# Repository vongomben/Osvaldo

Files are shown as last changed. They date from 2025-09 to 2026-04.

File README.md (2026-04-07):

# Osvaldo
Osvaldo is aimed to make ethreal messages physical, from the meshiverse:

Osvaldo

It all stems from **[a thought](https://www.reddit.com/r/meshtastic/comments/1d07e7j/meshtastic_thermal_printer_ticker_tape_node/) I had a year ago: how to save and somehow record these ephemeral-ethereal messages in our absence?**

Attach a printer to a meshtastic radio and see the messages coming one after another, a real physical representation of the conversations.

This project was an excuse to see how far a meshtastic radio could be integrated into a more distributed and complex system. 

A number of things can be built from here, including - in addition to the printer from which we start - **a small bot capable of field operations**, or even **a very simple BBS** (Bulletin board system) **based on microntrollers**. 

The idea of the printer is itself an hommage to the [Little Printer from Berg](https://www.failory.com/cemetery/berg) [Youtube Video](https://www.youtube.com/embed/IlC5taBgLp0?si=3HXCBTyb_Gr8--oA)

As for the Meshbot, this project updates several ideas and limits and scenarios in a new way. 
We are not making "printer of the internet", you could easily do that in many other ways-
Osvaldo is not even connected to the internet (and for this reason, I guess it doesn't event know the time and date). 
Osvaldo is connected to the Mesh. 

He receives messages and prints them. 
I could possibly add many features to this, which is an ongoing project. 
One is the Battery, maybe even solar powered. 
Another is exposing a Captive Portal that allows you to control Osvaldo via the phone (wifi): eyes (colours), texts, QR code of the Meshtastic Channel Osvaldo is listening to.

The future holds many challenges in front of us, lets see. 

### But What is Osvaldo doing right now?

- Osvaldo is a node in the Mesh
- Prints the received messages and make some funny LED patterns

### Hardware

- a meshtastic radio (I am using a [XIAO ESP32S3 & Wio-SX1262 Kit for Meshtastic & LoRa](https://www.seeedstudio.com/Wio-SX1262-with-XIAO-ESP32S3-p-5982.html?)
- a second radio from which to send data (paired with a cell phone)
- a microcontroller (Xiao ESP32S3)
- a voltage converter
- 2 switches (I want to be able to turn off the printer and possibly turn off the Xiao ESP32S3 managing the LEDS & printer behaviours)
- a strip of WS2812 LEDs
- 2 kikcback diodes (or Schottky diodes) because we will need to access both boards (the xiao-radio and tha xiao that manages the printer) without powering up the rest / interfere with the circuits. 
- two [Xiao Grove Shields](https://wiki.seeedstudio.com/Grove-Shield-for-Seeeduino-XIAO-embedded-battery-management-chip/) (for purely educational purposes - I'm getting old. You can skip them if you want to make you project tynier and save money. 

### Software side, we use:
- [meshtastic web flasher](https://flasher.meshtastic.org/)
- [meshtastic console](https://client.meshtastic.org/)
- [Arduino IDE with ESP32 core](https://wiki.seeedstudio.com/xiao_esp32s3_getting_started/#software-preparation)
- [Meshtastic's Protobuf library for Arduino](https://github.com/meshtastic/Meshtastic-arduino)
- [Adafruit Thermal Printer Library](https://github.com/adafruit/Adafruit-Thermal-Printer-Library) 

## 1) Flashing Radio n° 1

Visit [meshtastic web flasher](https://flasher.meshtastic.org/) and follow the instructions. 

flashing

## 2) Configuring the Radio

While you can go on from here using the Android or iOS app, I'll stick with the [meshtastic console](https://client.meshtastic.org/). 
We are going to **define its Serial pins** (based on Xiao's pin mapping) and **enable protobuf communication**. 

configuring

Since I'm using the [Xiao Grove Shields](https://wiki.seeedstudio.com/Grove-Shield-for-Seeeduino-XIAO-embedded-battery-management-chip/) I'm also sharing this useful image of the pin mapping. 

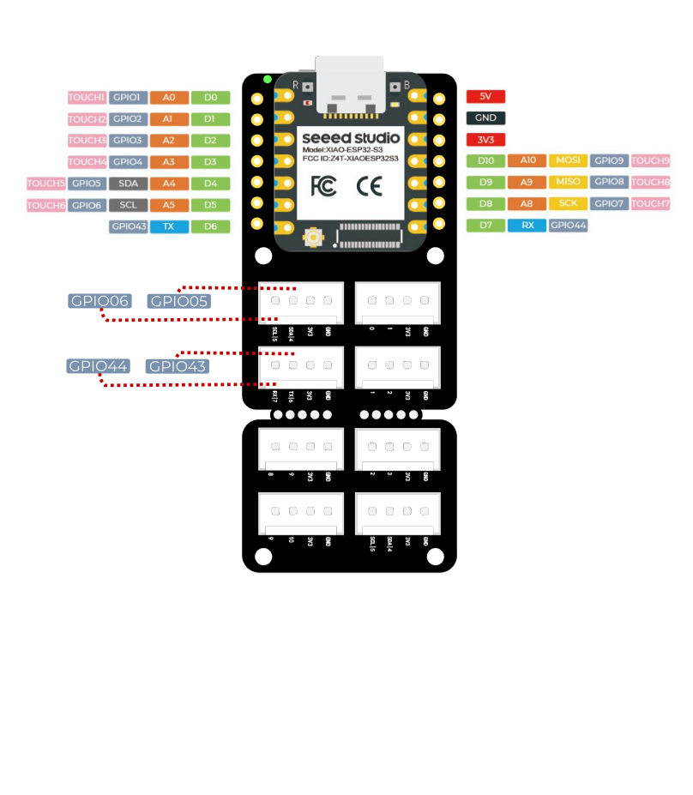
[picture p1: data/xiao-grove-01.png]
Xiao Grove Shield


## 3) Listening to the Serial Port using Protobuf from another Xiao

Let's connect the two boards in this way. 
Important TX is going to RX, and viceversa. Do not connect 3V3 for now. 

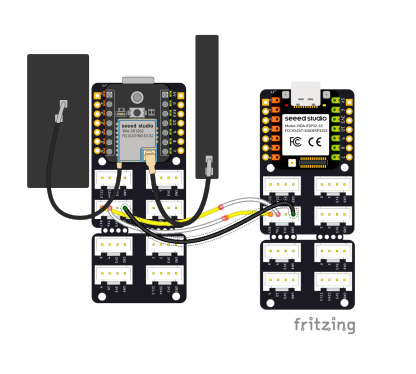
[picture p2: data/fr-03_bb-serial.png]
serial


In order to have a cable for the serial communication I changed a grove connector making it usable changing TX to RX and vice versa. 

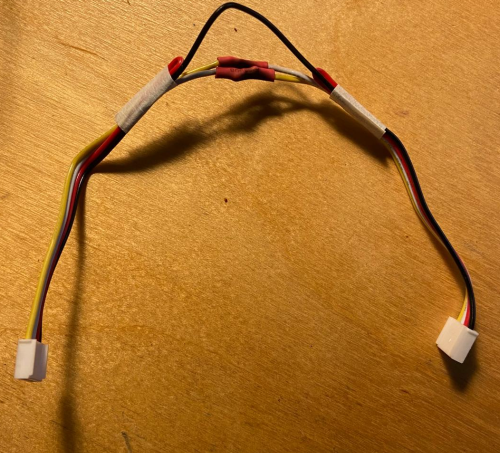
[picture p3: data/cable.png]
special cable


After installed the library, we can run this code in order to read whichever is passing via the serial and read all the nodes received in the serial port. Don't worry: we are going to fine tune this code in order to do less.

## 4) Let's attach the priter!

Hook up the printer following these instructions

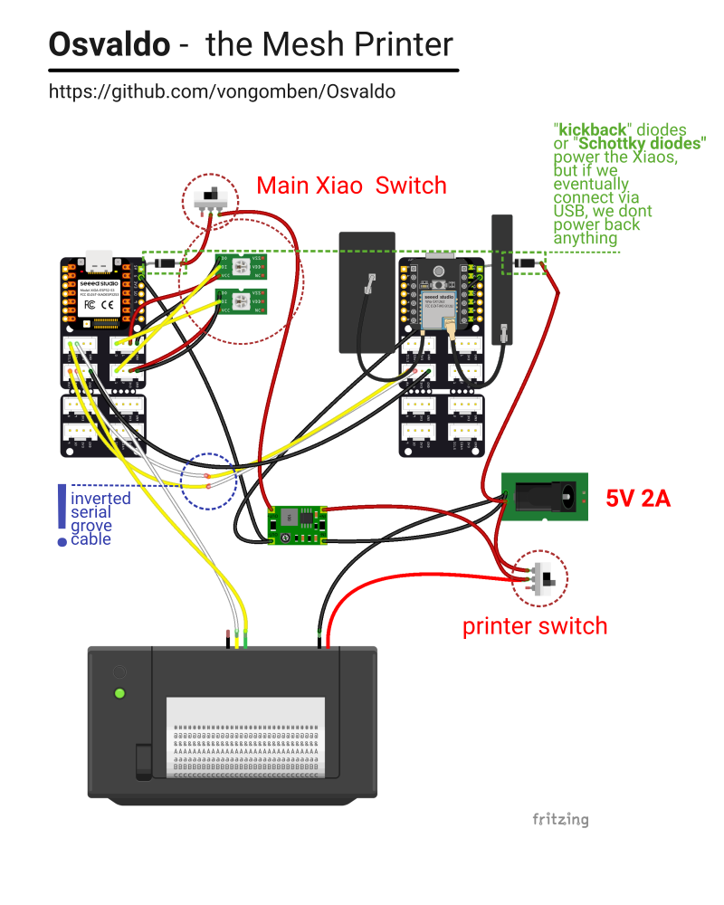
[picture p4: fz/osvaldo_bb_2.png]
printer


## 5) Print and assemble Osvaldo

I have used some trasparent PLA to create the eyes. Inside I've put the LEDs. 
Nice. 
You can find the stl files of this version in the folder. You should print "eye-cover.stl" in transparent PLA. All the rest is up to you for color or material.  

You have to solder the LEDs in order to make them stay in the eye. 

led

##  Test Osvaldo

Before connecting Osvaldo to the Mesh we have to test if it's printing and the LEDs are working:
- Check the LEDs
- check connections (passive listener)
- Test the final printer!

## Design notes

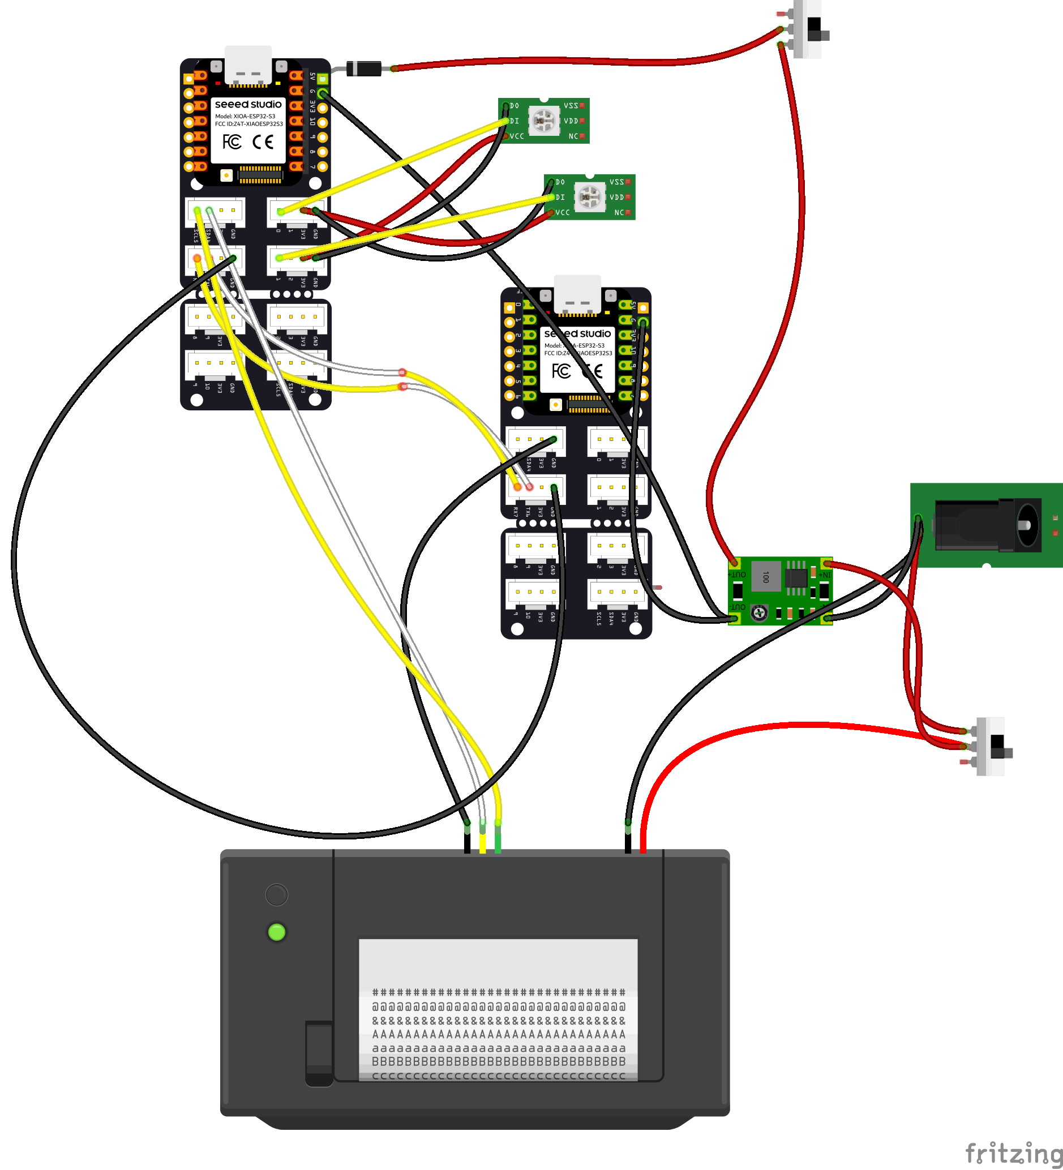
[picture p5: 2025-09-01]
fz/osvaldo_bb.png

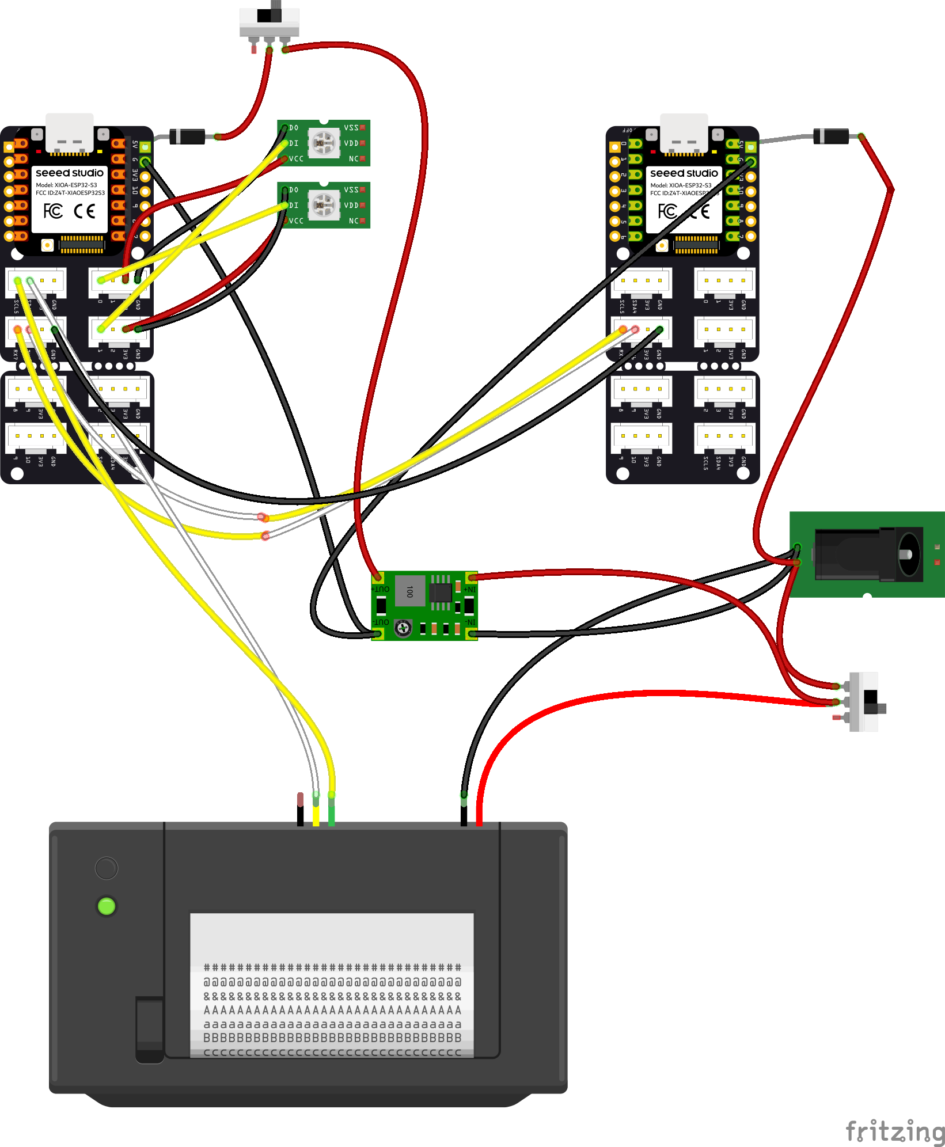
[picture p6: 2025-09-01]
fz/osvaldo_bb_3.png

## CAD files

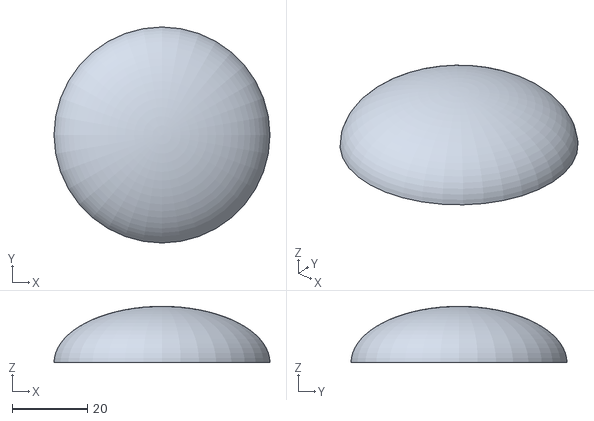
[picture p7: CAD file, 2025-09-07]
data/stl/eye-cover.stl
57.5 x 57.5 x 15.0

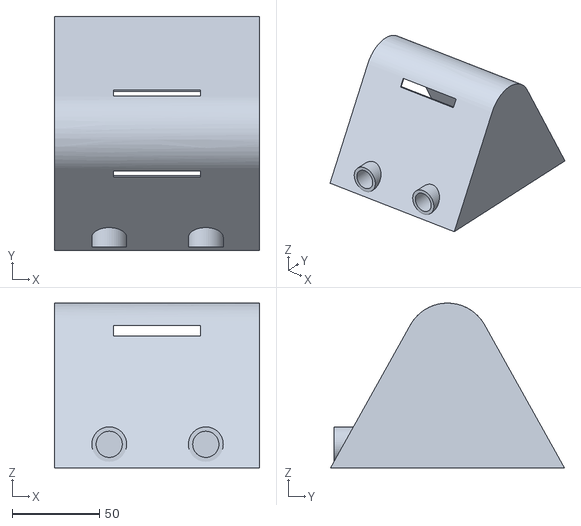
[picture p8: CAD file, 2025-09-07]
data/stl/back.stl
117.5 x 134.0 x 94.4

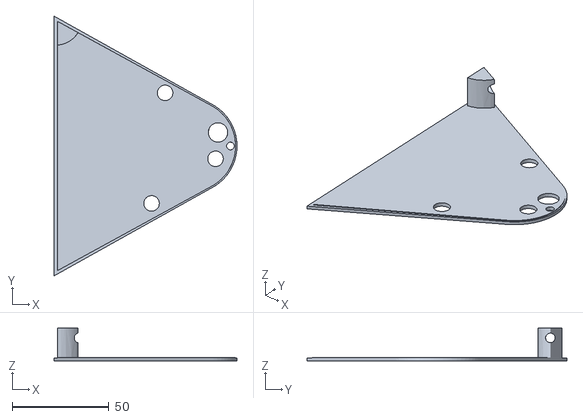
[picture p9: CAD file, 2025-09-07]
data/stl/side.stl
94.4 x 134.0 x 16.8

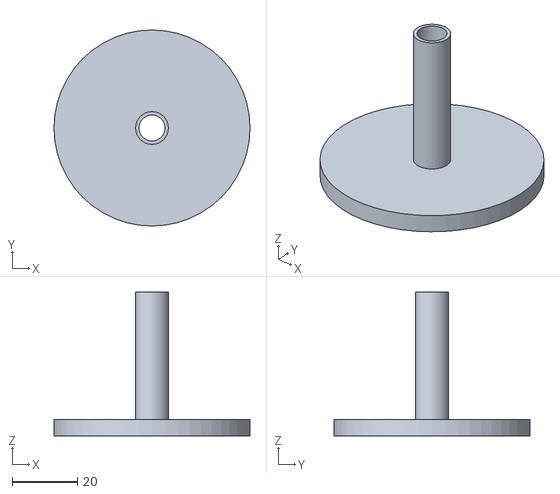
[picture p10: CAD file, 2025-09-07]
data/stl/eye.stl
60.0 x 60.0 x 44.0

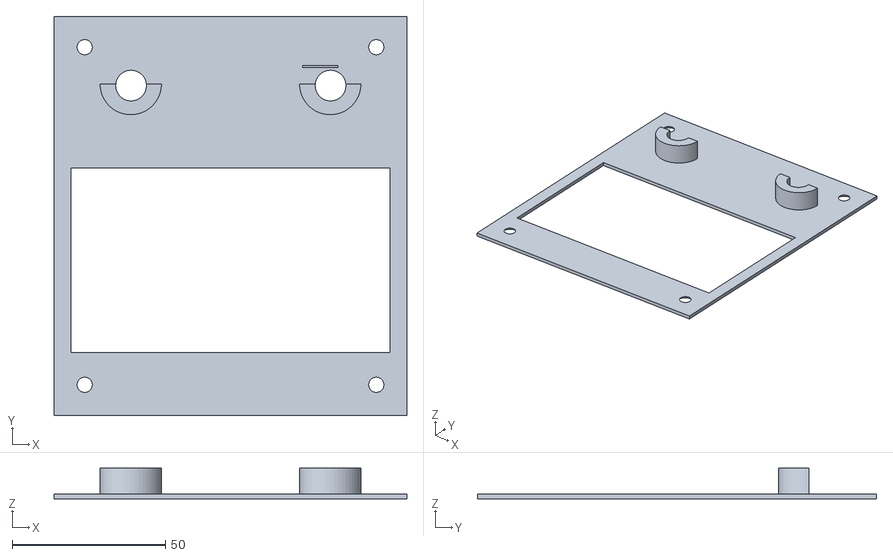
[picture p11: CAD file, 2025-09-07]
data/stl/front.stl
115.0 x 130.0 x 10.0

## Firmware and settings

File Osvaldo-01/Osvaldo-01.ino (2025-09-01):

// Meshita Sept 2025
// Osvaldo 01
// Printer v 0.10.2 (off-grid + boot/double rainbow)
// Meshtastic -> Thermal Printer (wrapping + upsideDown fix, no-CR) + LED rainbow with fade-out
//
// CHangelog: 1 rainbow at startup; 2 rainbows when Meshtastic radio answers (connected_callback)

#include <FastLED.h>
#include <Meshtastic.h>
#include "Adafruit_Thermal.h"
#include <esp_system.h>   // esp_reset_reason()

// ====== CONFIG ======
const bool   UPSIDE_DOWN         = true;   // true: upsideDownOn() & inverted lines
const uint8_t INTER_MESSAGE_FEED = 3;      // blank lines between messages
const uint8_t PRN_COLS           = 32;     // columns per row (font ‘S’ typically 32)

// Power
const uint16_t POWER_GOOD_MS     = 600;    // waiting to stabilize the bucks before printing
const uint16_t PRN_AFTER_UART_MS = 150;    // pause after Serial2.begin() before printer.begin()

// Diagnostic reset
#define DIAG_PRINT_TO_PRINTER 0   // 0=Serial only; 1=also print to printer (after init)
RTC_DATA_ATTR uint32_t bootCounter = 0;    // boot count as long as it remains powered

// ====== LED Stuff ======
#define DATA_PIN      D1
#define DATA_PIN2     D0
#define LED_TYPE      WS2812
#define COLOR_ORDER   GRB
#define NUM_LEDS      64

CRGB leds[NUM_LEDS];
CRGB leds2[NUM_LEDS];

#define BRIGHTNESS         96
#define FRAMES_PER_SECOND  120

// ====== Meshtastic UART (XIAO ESP32S3) ======
#define SERIAL_RX_PIN 44   // GPIO44 (RX from Meshtastic device)
#define SERIAL_TX_PIN 43   // GPIO43 (TX to Meshtastic device)
#define MESH_BAUD     9600

// ====== Thermal printer UART (Serial2) ======
// Note: Serial2.begin(baud, config, RX, TX) — the correct order is (RX, TX)!
#define PRN_RX   D4   // to   printer TX
#define PRN_TX   D5   // to printer RX
#define PRN_BAUD 19200

// ====== Periodic sending (optional) ======
#define SEND_PERIOD 300  // s
uint32_t next_send_time = 0;
bool not_yet_connected = true;

// ====== LED status / Effects ======
enum LedState { IDLE, RAINBOW, FADEOUT };
LedState ledState = IDLE;

bool startRainbowPending = false;
uint32_t rainbowStart = 0;
uint32_t fadeStart = 0;

const uint32_t rainbowDuration = 3000;  // ms
const uint32_t fadeDuration    = 1000;  // ms
uint8_t gHue = 0;
const uint8_t baseBrightness = BRIGHTNESS;

// ====== Printer ======
Adafruit_Thermal printer(&Serial2);

// ====== Coda stampa ======
const int PRINT_QUEUE_SIZE = 8;
String printQueue[PRINT_QUEUE_SIZE];
int qHead = 0, qTail = 0;

bool enqueuePrint(const String& s) {
  int next = (qHead + 1) % PRINT_QUEUE_SIZE;
  if (next == qTail) return false; // coda piena
  printQueue[qHead] = s;
  qHead = next;
  return true;
}
bool dequeuePrint(String &out) {
  if (qTail == qHead) return false; // vuota
  out = printQueue[qTail];
  qTail = (qTail + 1) % PRINT_QUEUE_SIZE;
  return true;
}

// --- helper: remove only spaces/tabs at the end of the line ---
static String rtrim(const String& in) {
  int end = in.length() - 1;
  while (end >= 0) {
    char c = in[end];
    if (c == ' ' || c == '\t') end--;
    else break;
  }
  if (end < 0) return String();
  return in.substring(0, end + 1);
}

// --- helper: normalizes common characters and terminators ---
static void normalizeCommon(String &s) {
  s.replace("\r\n", "\n");
  s.replace("\r", "\n");
  s.replace("\xC2\xA0", " ");   // NBSP -> space
  s.replace("\xE2\x80\x99", "'"); // ’
  s.replace("\xE2\x80\x98", "'"); // ‘
  s.replace("\xE2\x80\x9C", "\""); // “
  s.replace("\xE2\x80\x9D", "\""); // ”
}

// --- optional: UTF-8 accents -> “safe” ASCII (comment if you want to keep accents) ---
static String asciiFallback(String s) {
  s.replace("\xC3\xA0", "a"); s.replace("\xC3\xA8", "e"); s.replace("\xC3\xAC", "i");
  s.replace("\xC3\xB2", "o"); s.replace("\xC3\xB9", "u"); s.replace("\xC3\xA9", "e");
  s.replace("\xC3\x80", "A"); s.replace("\xC3\x88", "E"); s.replace("\xC3\x8C", "I");
  s.replace("\xC3\x92", "O"); s.replace("\xC3\x99", "U"); s.replace("\xC3\x89", "E");
  return s;
}

// --- helper: wrap a “logical” row with fixed columns, respecting the words ---
static void wrapLineToCols(const String& src, uint8_t cols, String outLines[], int &count, int maxLines) {
  int i = 0, N = src.length();
  while (i < N && count < maxLines) {
    while (i < N && src[i] == ' ') i++;
    int end = i + cols;
    if (end >= N) { outLines[count++] = rtrim(src.substring(i)); break; }
    int j = end;
    while (j > i && src[j] != ' ' && src[j] != '\t') j--;
    if (j == i) { outLines[count++] = rtrim(src.substring(i, end)); i = end; }
    else        { outLines[count++] = rtrim(src.substring(i, j));  i = j + 1; }
  }
}

// --- robust multi-line printing with PRN_COLS wrapping and upsideDown compensation ---
void printerPrintParagraph(String s) {
  normalizeCommon(s);
  // Comment if you want to keep the accents real:
  s = asciiFallback(s);

  const int MAX_LINES = 160;
  String logical[MAX_LINES];
  int ln = 0, start = 0;
  while (ln < MAX_LINES && start <= s.length()) {
    int nl = s.indexOf('\n', start);
    if (nl == -1) { logical[ln++] = rtrim(s.substring(start)); break; }
    logical[ln++] = rtrim(s.substring(start, nl));
    start = nl + 1;
  }
  if (ln > 0 && logical[ln - 1].length() == 0) ln--;

  String wrapped[MAX_LINES];
  int wn = 0;
  for (int i = 0; i < ln && wn < MAX_LINES; ++i) {
    if (logical[i].length() == 0) { wrapped[wn++] = ""; continue; }
    wrapLineToCols(logical[i], PRN_COLS, wrapped, wn, MAX_LINES);
  }

  String out; out.reserve(s.length() + wn + 8);
  if (UPSIDE_DOWN) { for (int i = wn - 1; i >= 0; --i) { out += wrapped[i]; if (i > 0) out += '\n'; } }
  else             { for (int i = 0; i < wn; ++i)     { out += wrapped[i]; if (i < wn - 1) out += '\n'; } }

  if (out.length() > 0) { printer.print(out); printer.write('\n'); }
  printer.feed(INTER_MESSAGE_FEED);
  Serial2.flush();
  delay(20);
}

// ====== Diagnostic reset ======
static const char* resetReasonToStr(esp_reset_reason_t r) {
  switch (r) {
    case ESP_RST_POWERON:   return "POWERON";
    case ESP_RST_EXT:       return "EXT_PIN";
    case ESP_RST_SW:        return "SOFTWARE";
    case ESP_RST_PANIC:     return "PANIC";
    case ESP_RST_INT_WDT:   return "INT_WDT";
    case ESP_RST_TASK_WDT:  return "TASK_WDT";
    case ESP_RST_WDT:       return "WDT";
    case ESP_RST_BROWNOUT:  return "BROWNOUT";
    case ESP_RST_SDIO:      return "SDIO";
    case ESP_RST_DEEPSLEEP: return "DEEPSLEEP";
    default:                return "UNKNOWN";
  }
}

void diagPrintReset(const char* where) {
  esp_reset_reason_t r = esp_reset_reason();
  bootCounter++;
  String msg = String("[DIAG] ") + where + " reset=" + resetReasonToStr(r) + " boot#=" + String(bootCounter);
  if (Serial) { Serial.println(msg); }
#if DIAG_PRINT_TO_PRINTER
  // Stampa solo se la stampante è già inizializzata e alimentazione stabile
  printer.println(msg); printer.feed(1);
#endif
}

// ====== Callback Meshtastic ======
void connected_callback(mt_node_t *node, mt_nr_progress_t progress) {
  if (not_yet_connected && Serial) Serial.println("✅ Connected to Meshtastic device!");
  not_yet_connected = false;
}

void text_message_callback(uint32_t from, uint32_t to, uint8_t channel, const char* text) {
  if (Serial) {
    Serial.print("📩 RX Meshtastic  From: "); Serial.print(from);
    Serial.print("  To: "); Serial.print(to);
    Serial.print("  Ch: "); Serial.print(channel);
    Serial.print("  Text: "); Serial.println(text);
  }
  startRainbowPending = true; // avvia LED
  String line = String(text);
  if (!enqueuePrint(line) && Serial) Serial.println("⚠️ Print queue full, dropping message.");
}

// ====== Setup ======
void setup() {
  Serial.begin(115200);
  // NO while(!Serial):  do not block in off-grid mode
  diagPrintReset("BOOT"); // log reason for reset

  // Meshtastic
  mt_serial_init(SERIAL_RX_PIN, SERIAL_TX_PIN, MESH_BAUD);
  mt_set_debug(false); // less spam
  mt_request_node_report(connected_callback);
  set_text_message_callback(text_message_callback);

  // LED
  delay(3000); // safety delay for LED
  FastLED.addLeds<LED_TYPE, DATA_PIN,  COLOR_ORDER>(leds,  NUM_LEDS).setCorrection(TypicalLEDStrip);
  FastLED.addLeds<LED_TYPE, DATA_PIN2, COLOR_ORDER>(leds2, NUM_LEDS).setCorrection(TypicalLEDStrip);
  FastLED.setBrightness(baseBrightness);
  FastLED.clear(); FastLED.show();

  // POWER-GOOD for regulators/lines before touching the printer
  delay(POWER_GOOD_MS);

  // Printer UART (ordine: RX,TX)
  Serial2.begin(PRN_BAUD, SERIAL_8N1, PRN_RX, PRN_TX);
  delay(PRN_AFTER_UART_MS);

  // Initialize printer (softer timing to reduce peaks)
  printer.begin();
  if (UPSIDE_DOWN) printer.upsideDownOn(); else printer.upsideDownOff();
  printer.wake();
  printer.setDefault();
  printer.setSize('S');    // max coloumns
  printer.justify('L');    // left align
  printer.setTimes(60, 6); // <-- REDUCED PEAKS compared to 80,2
  printer.println(F("Printer ready."));
  printer.feed(1);

#if DIAG_PRINT_TO_PRINTER
  // The power supply should now be stable: print the reset reason.
  diagPrintReset("POST-PRN");
#endif

  if (Serial) Serial.println("Ready.");
}

// ====== Rainbow effect on both strips ======
void rainbow() {
  fill_rainbow(leds,  NUM_LEDS, gHue, 7);
  fill_rainbow(leds2, NUM_LEDS, gHue, 7);
}

// ====== Main Loop ======
void loop() {
  uint32_t now = millis();

  // Process Meshtastic (triggers callbacks)
  bool can_send = mt_loop(now);

  // Start LED on new received message
  if (startRainbowPending) {
    startRainbowPending = false;
    ledState = RAINBOW;
    rainbowStart = now;
    gHue = 0;
    FastLED.setBrightness(baseBrightness);
    if (Serial) Serial.println("🌈 Rainbow START");
  }

  // LED Management
  switch (ledState) {
    case IDLE: break;
    case RAINBOW:
      gHue += 1;  rainbow();  FastLED.show();  FastLED.delay(1000 / FRAMES_PER_SECOND);
      if (now - rainbowStart >= rainbowDuration) { ledState = FADEOUT; fadeStart = now; if (Serial) Serial.println("🌗 Fade-out START"); }
      break;
    case FADEOUT: {
      uint32_t t = now - fadeStart;
      if (t >= fadeDuration) { FastLED.clear(); FastLED.setBrightness(baseBrightness); FastLED.show(); ledState = IDLE; if (Serial) Serial.println("🟤 Fade-out STOP (off)"); }
      else {
        float progress = (float)t / (float)fadeDuration;
        uint8_t b = (uint8_t)((1.0f - progress) * baseBrightness); if (b == 0) b = 1;
        FastLED.setBrightness(b); FastLED.show(); FastLED.delay(1000 / FRAMES_PER_SECOND);
      }
    } break;
  }

  // Print: empty the queue (one per iteration so as not to block the LEDs)
  String toPrint;
  if (dequeuePrint(toPrint)) {
    printer.wake();
    printer.setDefault();
    printer.setSize('S');
    printer.justify('L');
    printerPrintParagraph(toPrint);
    if (Serial) { Serial.print("🖨️ Printed: "); Serial.println(toPrint); }
  }

  // (optional) periodic broadcast sending
 // if (can_send && now >= next_send_time) {
 //   mt_send_text("Hello from Xiao ESP32!", BROADCAST_ADDR, 0);
 //   next_send_time = now + SEND_PERIOD * 1000;
 // }
}

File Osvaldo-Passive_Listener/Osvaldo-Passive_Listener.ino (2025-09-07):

/*
  Meshtastic Serial-only passive listener
  - Connects via UART to a Meshtastic node (Protobuf API)
  - Prints any received text messages to USB Serial
  - Does NOT send anything
*/

#include <Meshtastic.h>

// --- USB serial for logs ---
#define USB_BAUD        9600

// --- UART to Meshtastic device ---
#define SERIAL_RX_PIN   44        // GPIO44 (RX from Meshtastic)
#define SERIAL_TX_PIN   43        // GPIO43 (TX to Meshtastic)
#define MESH_BAUD       9600      // Match your node setting

// --- Helper: strip non-printable for cleaner logs ---
static void print_clean(const char* s) {
  while (*s) {
    char c = *s++;
    if ((c >= 32 && c <= 126) || c == '\n' || c == '\r' || c == '\t') {
      Serial.print(c);
    } else {
      Serial.print('?');
    }
  }
}

// --- Text message RX callback ---
void text_message_callback(uint32_t from, uint32_t to, uint8_t channel, const char* text) {
  Serial.println("=== RX TEXT MESSAGE ===");
  Serial.print("From: ");    Serial.println(from);
  Serial.print("To: ");      Serial.println(to);
  Serial.print("Channel: "); Serial.println(channel);
  Serial.print("Text: \"");  print_clean(text); Serial.println("\"");
  Serial.println("=======================");
}

void setup() {
  Serial.begin(USB_BAUD);
  delay(50);
  Serial.println();
  Serial.println("=== Meshtastic Serial-only passive listener ===");
  Serial.print("UART RX="); Serial.print(SERIAL_RX_PIN);
  Serial.print(" TX=");     Serial.print(SERIAL_TX_PIN);
  Serial.print(" Baud=");   Serial.println(MESH_BAUD);

  // Init UART link
  mt_serial_init(SERIAL_RX_PIN, SERIAL_TX_PIN, MESH_BAUD);

  // Optional: set to true if you want to see heartbeats etc.
  mt_set_debug(false);

  // Register callback for text messages
  set_text_message_callback(text_message_callback);

  Serial.println("Setup complete. Listening for incoming text messages...");
}

void loop() {
  uint32_t now = millis();
  mt_loop(now);  // drive state machine, triggers callbacks on RX
}
